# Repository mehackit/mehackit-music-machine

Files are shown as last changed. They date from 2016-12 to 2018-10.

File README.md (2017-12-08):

# Mehackit Music Machine Shield

Music Machine is an Arduino shield that takes in MIDI and controls solenoids and servo motors. You can chain 4 Music Machine Shields and choose the corresponding MIDI notes with a DIP switch. One shield can drive 7 solenoids and 2 servo motors.

See Music Machine Manual for instructions. Currently only in Finnish.

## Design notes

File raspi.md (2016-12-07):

# Raspberry Pi

## Connecting with SSH via ethernet on OSX

- IP = 	192.168.2.2

- Install XQuartz

- Check internet preferences

- Plug the ethernet cable, plug power to the Raspberry Pi

- Terminal: ```ssh -X pi@192.168.2.2```

- Password: raspi

- Copy local pd-path to raspi:

  - Open a new terminal tab on your own computer and locate the file you want to send.
  - ```scp patch.pd pi@192.168.2.2:/some/remote/directory/ ```

- Open the patch on raspi:

  - ```pd-extended patch.pd```

- Open the patch on startup:

  - open .bashrc: ```nano ~/.bashrc```
  - add: ```pd-extended -nogui /path/to/patch.pd```

- Reboot: ```sudo reboot```

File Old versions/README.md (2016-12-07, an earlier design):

# Mehackit Music Machine

## V1

https://vimeo.com/158470330

The first incarnation of the Mehackit music machine was at the Espoo Museum of Modern Art during the Mehackit Art Hack event. 

There's a Pure Data sequencer running on the Raspberry Pi, that sends serial messages to the chan of Arduinos. Each arduino checks if the message belongs to them and either triggers a corresponding solenoid/motor or passes the message forward.

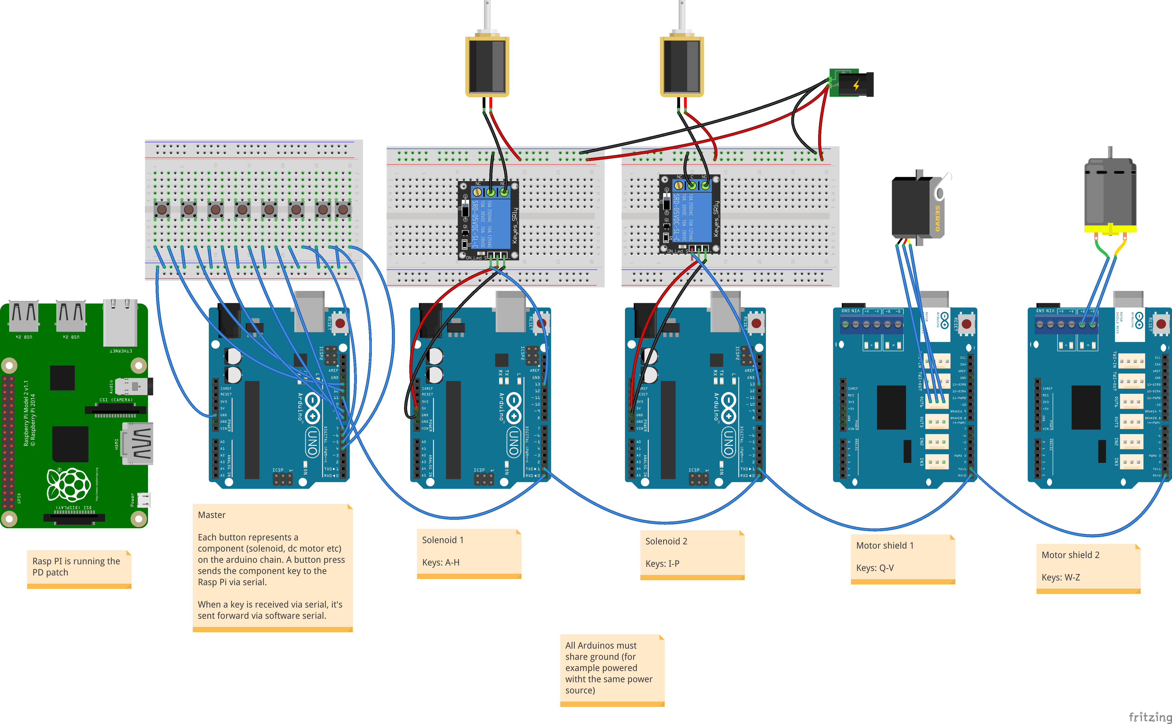
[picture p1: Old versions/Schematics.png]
layout


 The controller looked like this:

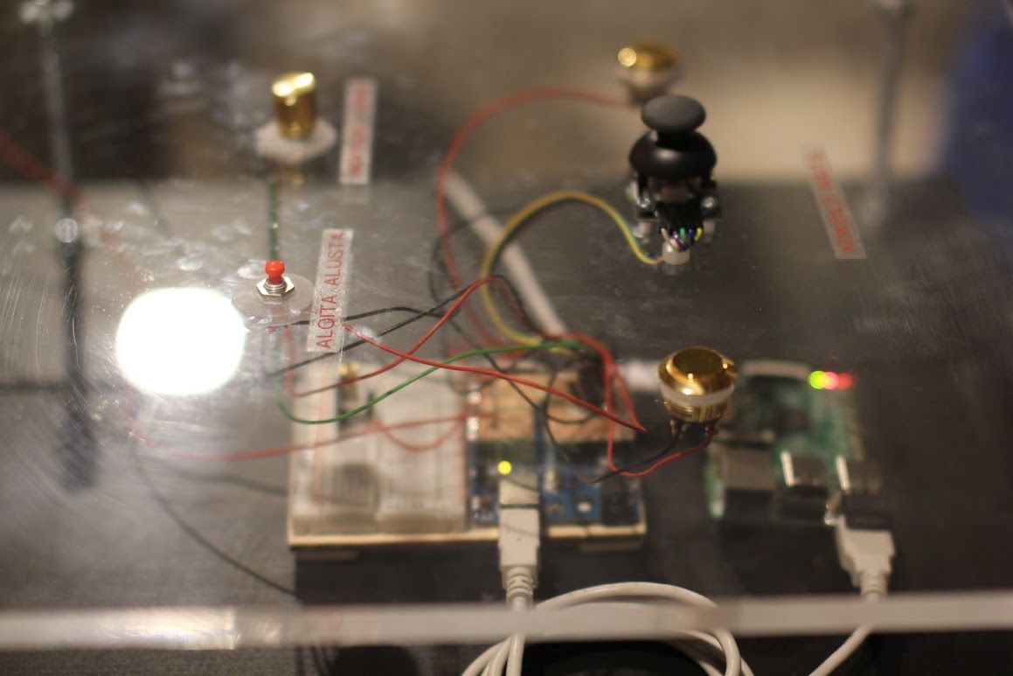
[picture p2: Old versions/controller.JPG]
controller
 

This is the finished installation:

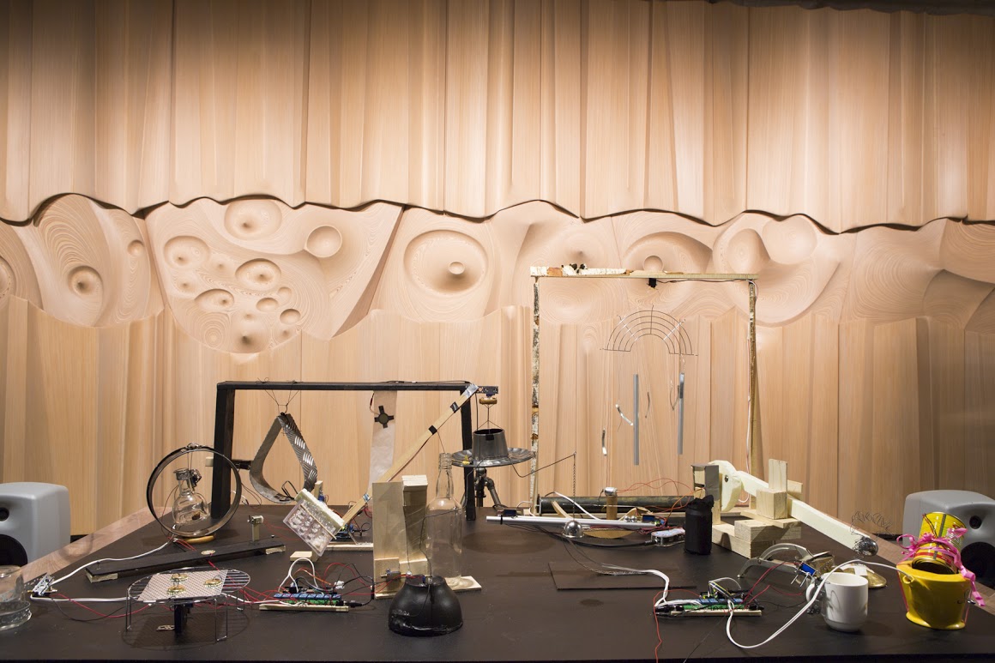
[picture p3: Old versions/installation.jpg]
installation


## V2

New version of the music machine, now with more buttons!

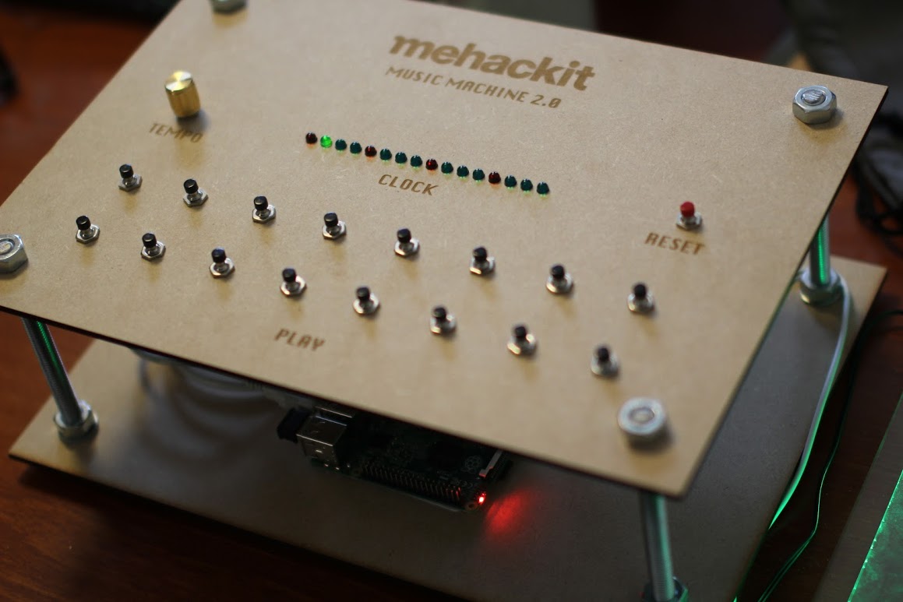
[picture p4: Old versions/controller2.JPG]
controller2


## V3

New version of the music machine, now with less buttons! 

https://vimeo.com/194648696

This version has four knobs that each control a pair of solenoids. The knobs choose from 10 different predefined patterns. The patterns mimic house-like kick, snare, hi-hat and percussion patterns.

## music_machine_v3

The inspiration came from a Max for Live device called Instant Haus by Alexkid. The aim for the controller is to make the installation sound good immediately when a user twists the knobs but still offer enough control to express themselves and play the installation.

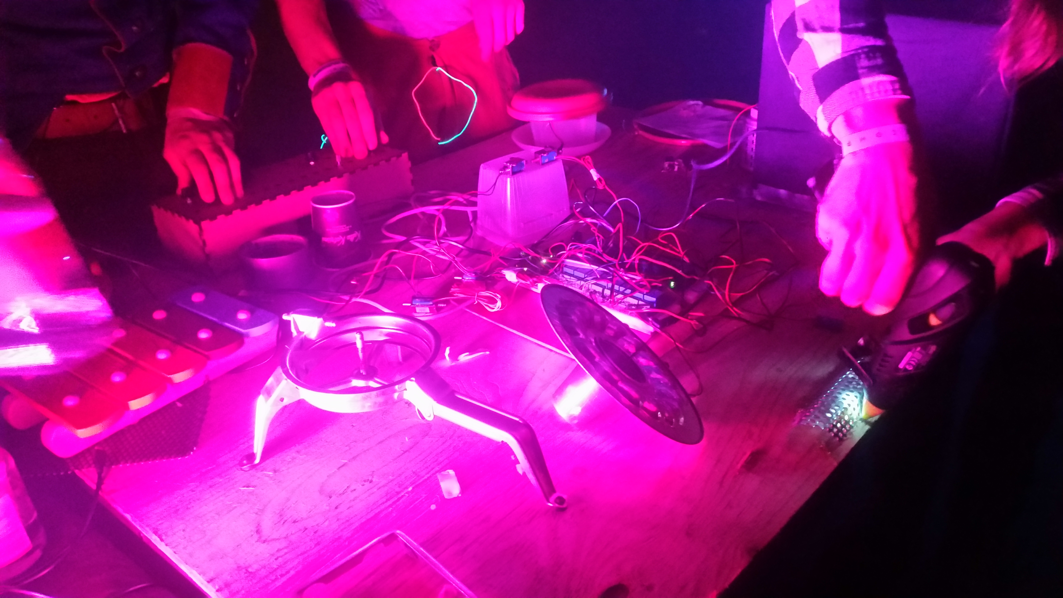
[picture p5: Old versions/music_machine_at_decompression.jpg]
music_machine_at_decompression


This version uses Teensy 3.0 to read the knobs. The Teensy is set up as an USB-MIDI device so it communicates with the Pure Data patch running on Raspberry Pi via MIDI. The Pd-patch then sends the 'notes' to the Arduino as chars via serial.

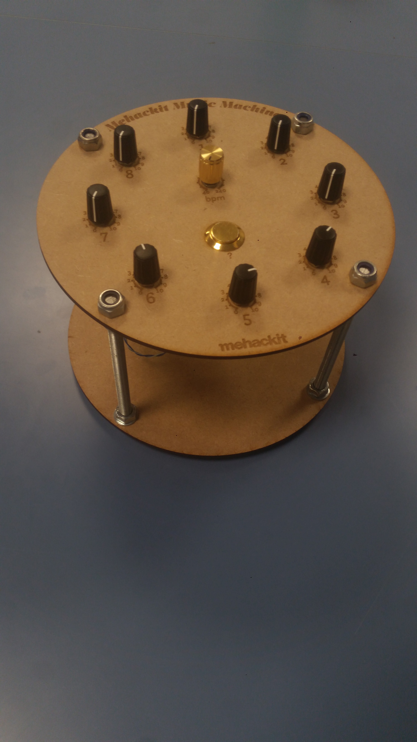
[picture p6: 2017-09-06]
controller4.jpg

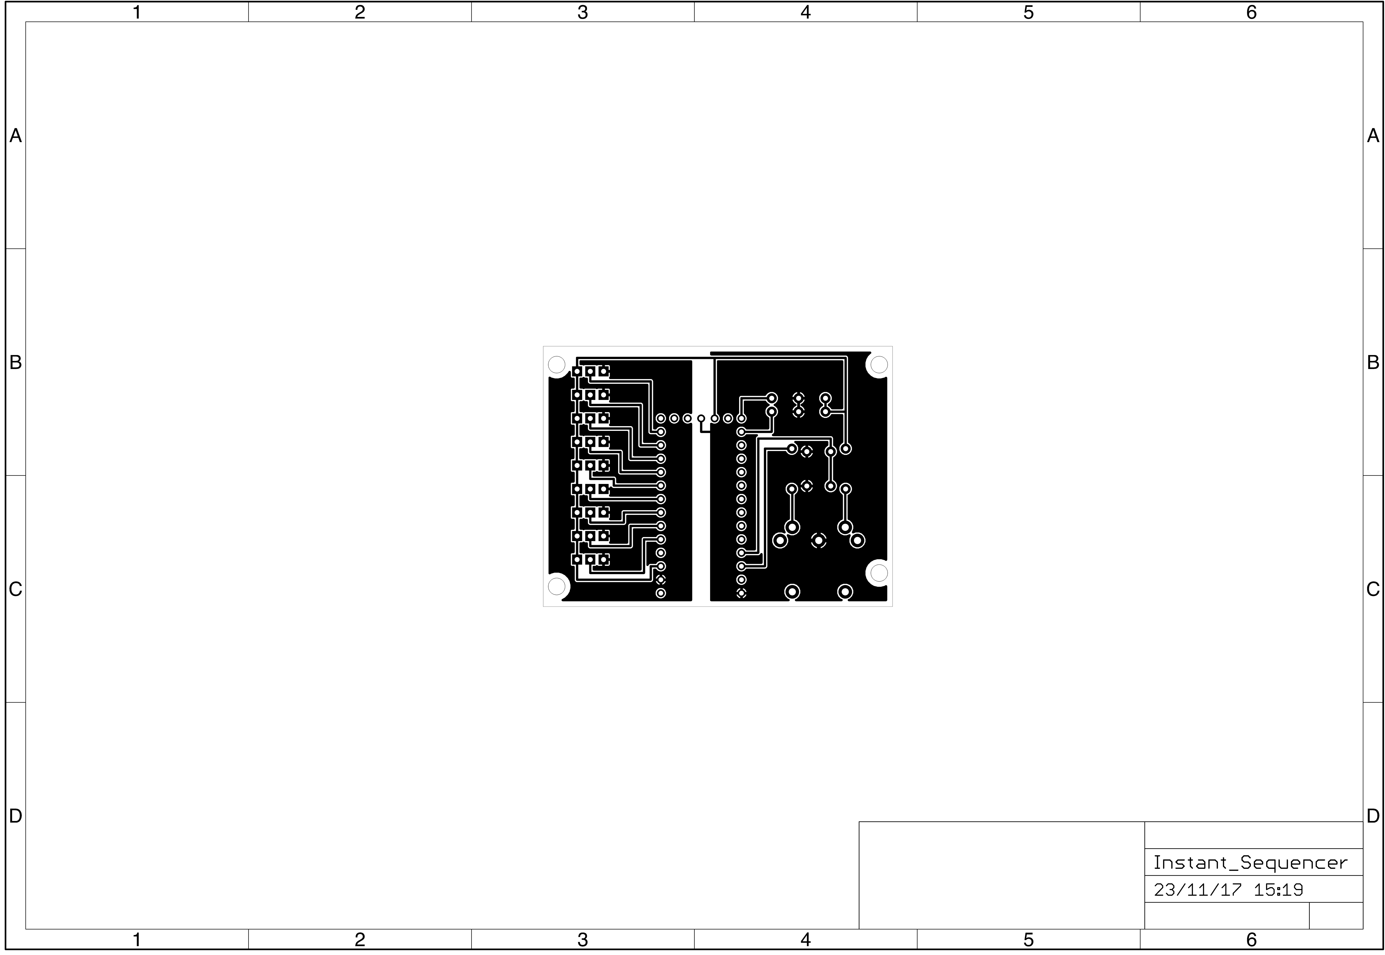
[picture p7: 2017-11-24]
PCB Files/Sequencer PCB.png

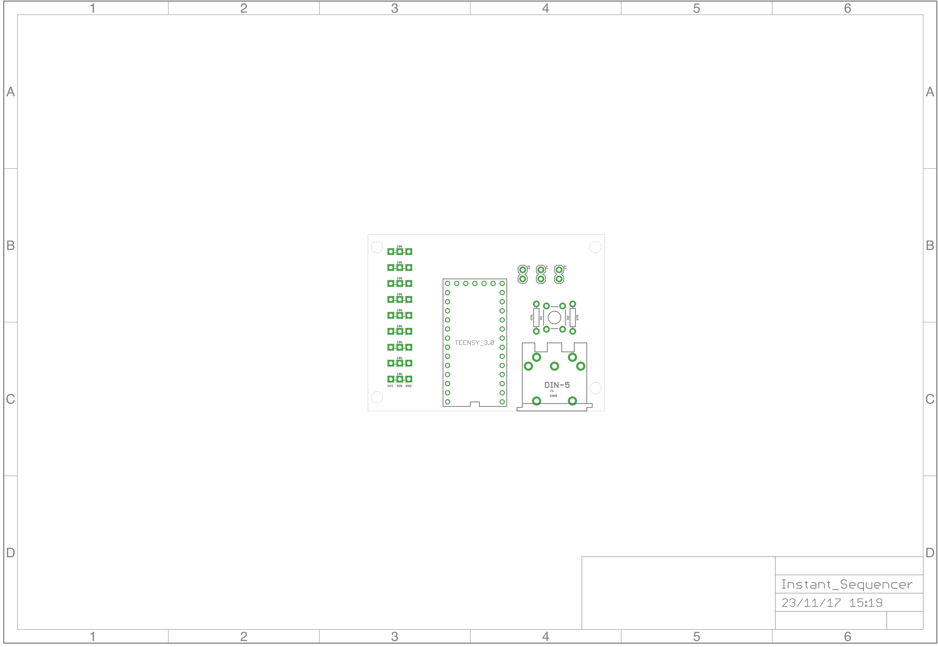
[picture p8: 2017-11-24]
PCB Files/Sequencer PCB placement.png

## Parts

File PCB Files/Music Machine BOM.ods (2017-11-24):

Qty | Package size | Value | TME.EU LINK | Name
1 | 2 | 2 Poles | https://www.tme.eu/en/details/ds-02/dip-switches/ninigi/ | 2 DIP SWITCH
2 | 50 | 10uF | https://www.tme.eu/en/details/ce-1_50sp/85c-tht-electrolytic-capacitors/sr-passives/ | CAP
1 | 1 | ULN2003AN | https://www.tme.eu/en/details/uln2003an/drivers-integrated-circuits/texas-instruments/ | DARLINGTON ARRAY
2 | 1 | MIDI IN, MIDI THROUGH | https://www.tme.eu/en/details/mab5shsw/din-connectors/hirschmann/931744500-mab-5-sh-sw/ | DIN MIDI
1 | 20 | 1N914 | https://www.tme.eu/en/details/1n914tr/tht-universal-diodes/on-semiconductor-fairchild/ | DIODE
7 | 10 | 1N4001 | https://www.tme.eu/en/details/1n4001-dio/tht-universal-diodes/diotec-semiconductor/1n4001/ | DIODE
1 | 10 | DIP16 SOCKET | https://www.tme.eu/en/details/icvt-16p/standard-dip-sockets/connfly/ds1009-16at1nx/ | DIP SOCKET
2 | 5 | RED | https://www.tme.eu/en/details/osnr3134a/tht-leds-3mm/optosupply/ | LED
1 | 10 | SPST | https://www.tme.eu/en/details/tact-64n-f/microswitches-tact/ninigi/ | Momentary Switch
7 | 1 | CL1382B | https://www.tme.eu/en/details/cl1382/jack-connectors/cliff/s6bb-cl1382/ | MONO JACK
1 | 1 | 6N138 | https://www.tme.eu/en/details/6n138-l/optocouplers-analog-output/liteon/6n138/ | OPTOCOUPLER
5 | 10 | 1X10 | https://www.tme.eu/en/details/zl201-10g/pin-headers/connfly/ds1021-1_10sf11/ | Pin Header
2 | 1 | DC 5,5/2,5 | https://www.tme.eu/en/details/pj-102bh/dc-power-connectors/ | POWER JACK
1 | 5 | DC 5,5/2,5 | https://www.tme.eu/en/details/pc-004/dc-power-connectors/ | POWER PLUG
1 | 1 | 12V 1A DC 5,5/2,5 | https://www.tme.eu/en/details/zsi-50030/wall-mounted-power-supplies/qoltec/50030/ | Power supply
1 | 100 | 10k | https://www.tme.eu/en/details/m0.4w-10k/04w-metal-film-tht-resistors/royal-ohm/mff04ff1002a5/ | Resistor
5 | 100 | 220R | https://www.tme.eu/en/details/m0.4w-220r/04w-metal-film-tht-resistors/royal-ohm/mff04ff2200a5/ | RESISTOR
1 | 100 | 470R | https://www.tme.eu/en/details/m0.4w-470r/04w-metal-film-tht-resistors/royal-ohm/mff04ff4700a50/ | RESISTOR
7 | 1 | 12V 0.4A Push/Pull Solenoid |  | Solenoid
1 | 2 | LM7805 | https://www.tme.eu/en/details/lm7805act/unregulated-voltage-regulators/on-semiconductor-fairchild/ | VOLTAGE REGULATOR
7 | 2 | MONO PLUG | https://www.tme.eu/en/details/jc-139/jack-connectors/ | MONO PLUG

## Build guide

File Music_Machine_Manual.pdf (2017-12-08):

# MUSIC MACHINE MANUAL

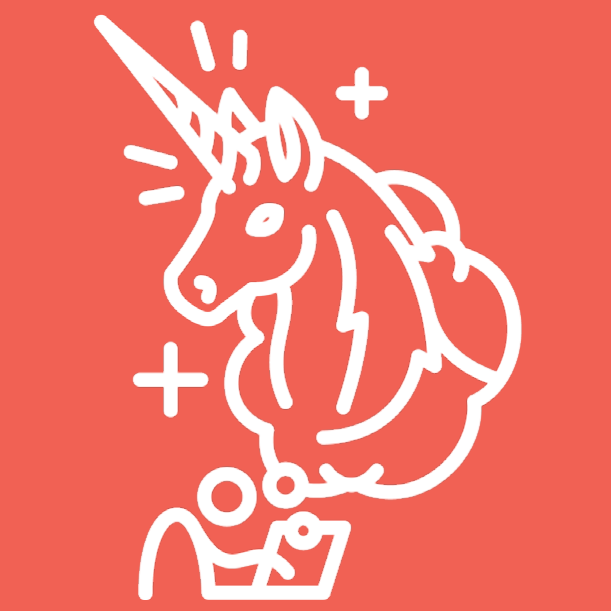
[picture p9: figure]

# MUSIC MACHINE

Music Machine on työkalu ääniveistosten luomiseen. Se kannustaa tutkimaan arkipäiväisten esineiden ja objektien äänimaailmaa muuttaen tavanomaiset asiat perkussiivisiksi soittimiksi.

Music Machine Shield toimii yhdessä Arduino Uno yhteensopivan mikrokontrollerin (esimerkiksi Mehackit Maker Board) kanssa ja vastaanottaa MIDI-viestejä esimerkiksi tietokoneelta tai MIDI-koskettimista.

Tämä opas esittelee Music Machine työpajarungon, käyttöohjeet sekä rakennusohjeet. Uusimmat päivitykset löytyvät Music Machinen github-sivuilta, osoitteesta github.com/mehackit/mehackit-music-machine. (https://github.com/mehackit/mehackit-music-machine/)

# Sisällysluettelo

Työpajan kulku | 1
Käyttöohjeet | 3
Rakennusohjeet | 5
Esimerkkiasennus | 7

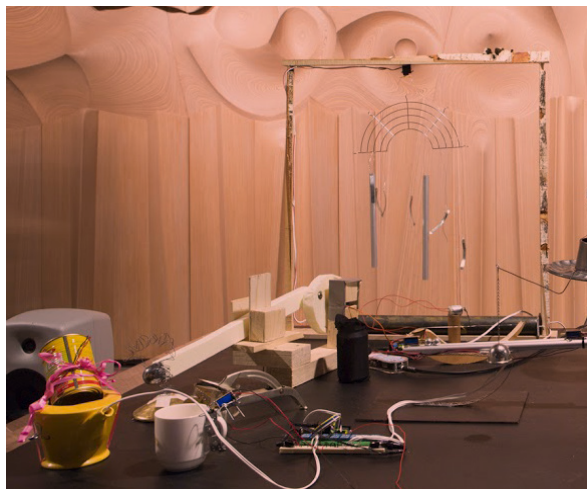
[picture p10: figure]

# Tarvikkeet

Määrä | Nimi
1 | Music Machine Shield PCB
1 | 10kΩ vastus (https://www.tme.eu/en/details/m0.4w-10k/04w-metal-film-tht-resistors/royal-ohm/mff04ff1002a5/)
5 | 330Ω vastus (https://www.tme.eu/en/details/m0.4w-220r/04w-metal-film-tht-resistors/royal-ohm/mff04ff2200a5/)
1 | 470Ω vastus (https://www.tme.eu/en/details/m0.4w-470r/04w-metal-film-tht-resistors/royal-ohm/mff04ff4700a50/)
2 | 10uF kondensaattori (https://www.tme.eu/en/details/ce-1_50sp/85c-tht-electrolytic-capacitors/sr-passives/)
1 | 1N914 vdiodi (https://www.tme.eu/en/details/1n914tr/tht-universal-diodes/on-semiconductor-fairchild/)
7 | 1N4001 diodi (https://www.tme.eu/en/details/1n4001-dio/tht-universal-diodes/diotec-semiconductor/1n4001/)
1 | LM7805 regulaattori (https://www.tme.eu/en/details/lm7805act/unregulated-voltage-regulators/on-semiconductor-fairchild/)
1 | 2 DIP-kytkin (https://www.tme.eu/en/details/ds-02/dip-switches/ninigi/)
1 | ULN2003AN darlington array IC (https://www.tme.eu/en/details/uln2003an/drivers-integrated-circuits/texas-instruments/)
1 | DIP16 kanta (https://www.tme.eu/en/details/icvt-16p/standard-dip-sockets/connfly/ds1009-16at1nx/)
2 | DIN-midi -liitin (https://www.tme.eu/en/details/mab5shsw/din-connectors/hirschmann/931744500-mab-5-sh-sw/)
2 | 3mm LED (https://www.tme.eu/en/details/osnr3134a/tht-leds-3mm/optosupply/)
1 | SPST painonappi (https://www.tme.eu/en/details/tact-64n-f/microswitches-tact/ninigi/)
1 | 6N138 optocoupler IC (https://www.tme.eu/en/details/6n138-l/optocouplers-analog-output/liteon/6n138/)
5 | 1x10 piikkirima (https://www.tme.eu/en/details/zl201-10g/pin-headers/connfly/ds1021-1_10sf11/)
2 | DC 5,5/2,5 -liitin (https://www.tme.eu/en/details/pj-102bh/dc-power-connectors/)
7 | 3,5mm mono-liitin (https://www.tme.eu/en/details/cl1382/jack-connectors/cliff/s6bb-cl1382/)
7 | 3,5mm mono-plugi (https://www.tme.eu/en/details/jc-139/jack-connectors/)
Muu
1 | Arduino Uno / Maker Board
1 | 12V 1A DC 5,5/2,5 Virtalähde (https://www.tme.eu/en/details/zsi-50030/wall-mounted-power-supplies/qoltec/50030/)
7 | 12V olenoidi
1 | MIDI-soitin DIN lähdöllä. (Esim Mu-sic Machine Sequencer)
1 | DIN-midi kaapeli
| Astioita,romua ym. soittimiksi

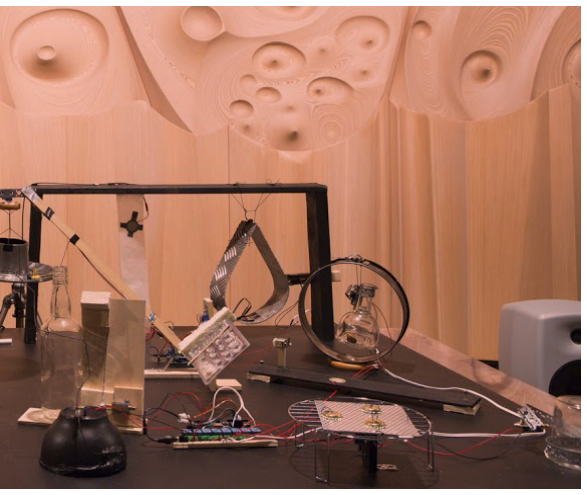
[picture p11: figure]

Työpajan tavoitteena on tutustua ääneen ilmiönä, herkistyä ympäröivien äänien kuuntelemiselle ja analysoinnille sekä toteuttaa kokeellinen ääniveistos kierrätysmateriaalein.

Teemaa voi jatkaa tutustumalla taiteilijoihin, kuten Jean Tinguely, Thessia Machado, Peter Vogel ja Alexander Calder, sekä tutustumalla tarkemmin Arduino-ympäristöön osoitteessa learn.mehackit.org

Aloitus (5min)
Toivota osallistujat tervetulleeksi ja esittäydy. Kerro työpajan sisällöstä ja näytä esimerkkinä yksi solenoidilla tehty soitin. Kysy osallistujien musiikkiharrastuksista.

Mitä ääni on (10min)
Pyydä osallistujia määrittelemään ääni. Ääni syntyy, kun jokin pinta värähtelee ja välittäjäaine (esimerkiksi ilma) välittää värähtelyn kuulijan korvaan. Työpajassa ääni syntyy, kun moottori kopauttaa esinettä, ja esine värähtelee.

Miten ääntä voi kuvailla? Työpajajassa ääntä kuvaillaan kolmella ominaisuudella: äänenkorkeus, voimakkuus sekä sävy. Tee seuraavaksi kaksi kuunteluharjoitusta, jotka puretaan kuvailemmalla kuultuja ääniä edellä mainituilla ominaisuuksilla.

Kuunteluharjoitus 1: Jokainen sulkee silmänsä ja kuuntelee ympäröiviä ääniä 60 sekunnin ajan. Kysy harjoituksen jälkeen, mitä ääniä osallistujat kuulivat.

Kuunteluharjoitus 2: Jokainen sulkee silmänsä ja kuuntelee ympäröiviä ääniä 60 sekunnin ajan sekä tuottaa yhden äänen harjoituksen aikana.

Soittimen rakennus (20min)
Tehtänä on tutkia ympäristöstä löytyvien esineiden akustisia ominaisuuksia ja rakentaa esineestä soitin moottorin avulla. Kannusta osallistujia pohtimaan äänen ominaisuuksia. Esimerkiksi bassorumpu on matala, kovaääninen ja kumiseva. Bassorumpua muistuttavan äänen

# TYÖPAJAN KULKU

luomiseksi pitäisi siis käyttää kookasta ja matalaäänistä esinettä.

Näytä esimerkkinä, miten moottorin voi kiinnittää esineesen. Jaa osallistujat pareihin ja anna jokaiselle parille yksi moottori. Kun sopiva esine löytyy, pari voi viimeistellä ja koristella soittimensa. Osoita pöytä, johon valmiit soittimet tuodaan ja johon installaatio rakentuu. Auta valmiita pareja kiinnittämään soittimen moottorin johdot Music Machineen.

Loppukonsertti (15min)
Kerää osallistujat yhteen, kun soittimet ovat valmiina. Pyydä vapaaehtoinen, joka pääsee esittämään ensi-esityksen. Esityksen jälkeen kuunnellaan vielä jokainen soitin erikseen ja tekijät pääsevät kertomaan luomuksestaan.

Esittelyjen jälkeen jokainen pääsee vuorollaan kokeilemaan laitteen käyttöä.

Lopetus (5min)
Siivoa lopuksi yhdessä osallistujien kanssa pahimmat sotkut. Kiitä työpajasta ja kannusta kuuntelemaan ympäristön ääniä esimerkiksi rullaportaissa, luonnossa, julkisissa liikennevälineissä jne.

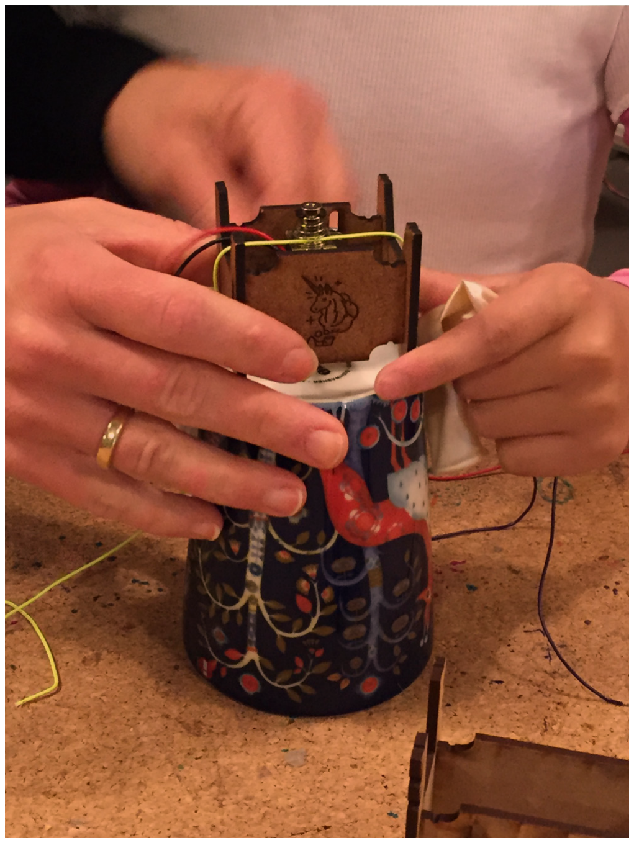
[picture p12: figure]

Lataa Arduino IDE osoitteesta arduino.cc. (https://www.arduino.cc/en/Main/Software) Lataa tiedost 'Music_Machine_Controller. ino' onoitteesta github.com/mehackit/mehackit-music-machine. (https://github.com/mehackit/mehackit-music-machine/) Kytke Arduino-yhteensopiva mikrokontrolleri tietokoneesen USB-johdolla, avaa edellä mainittu tiedosto Arduino IDE:llä ja lataa ohjelma mikrokontrollerille.

Paina Music Machine Shield varovasti mikrokontrollerin päälle. Valitse dip-kytkimellä kuunneltavien nuottien alue ja kytke MIDI-piuha MIDI-lähteeseen, kuten sekvensseriin, koskettimiin tai tietokoneeseen. Dip-kytkimen käyttö selitetään tarkemmin sivun lopussa.

Kytke solenoidit 3,5mm liittimillä s-kirjaimella merkittyihin lähtöihin ja servo-moottorit piikkirimaliittimiin. Varmista, että servo-moottorin liitännät menevät oikein.

Liitä lopuksi virtalähde Music Machine Shieldiin.

Nuottialueen valitseminen

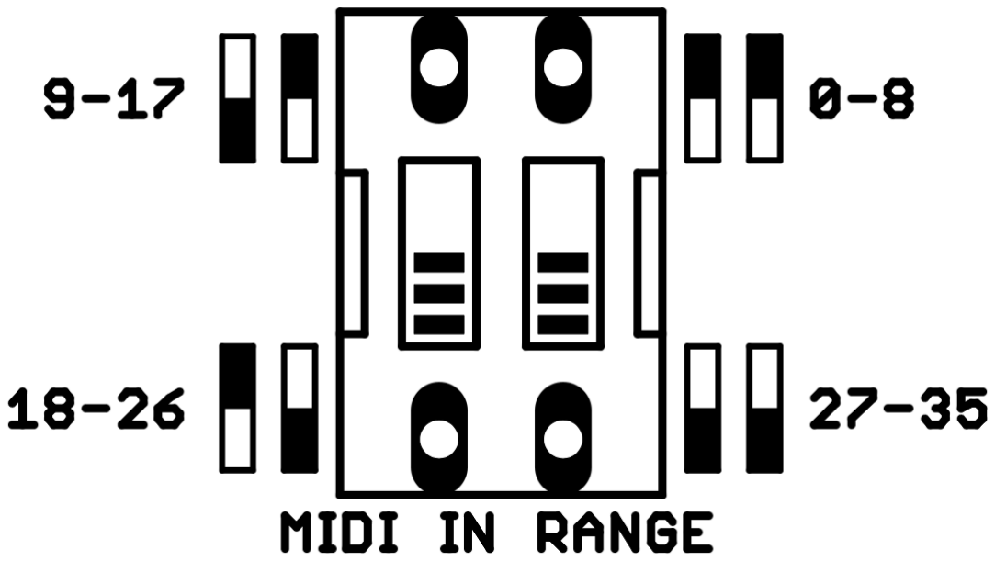
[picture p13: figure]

Nuottialue valitaan asettamalla dip-kytkin yhteen neljästä mahdollisesta asennosta. Molempien liukujen ollessa ylhäällä, MIDI-nuotit 0-8 laukaisevat solenoidin tai moottorin. Asentoa vastaavat nuottialueet on merkattu kytkimen viereen. Mikrokontrolleri pitää käynnistää uudestaan kytkimen asennon muuttamisen jälkeen.

Halutessasi voit ketjuttaa usean soittimen MIDI-trough liitännän avulla ja asettaa soittimet kuuntelemaan eri nuottialueita.

# KÄYTTÖ-OHJEET

# MIDI-sekvensseri

Voit käyttää Music Machinen kanssa mitä tahansa MIDI-laitetta, jossa on lähtö DIN-kaapelille:

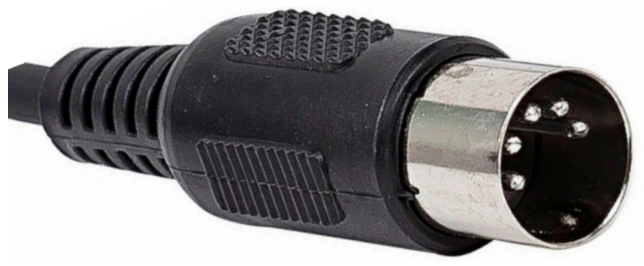
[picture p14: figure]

Useissa koskettimissa voi olla DIN-lähtö. Tietokoneesen voi liittää ulkoisen äänikortin tai MIDI-liitännän, jonka avulla eri musiikkiohjelmistoista voi lähettää MIDI-nuotteja.

Edellä mainitusta github-osoitteesta (https://github.com/mehackit/mehackit-music-machine/) löytyy lisäksi varta vasten Music Machinelle tehty MIDI-sekvensseri:

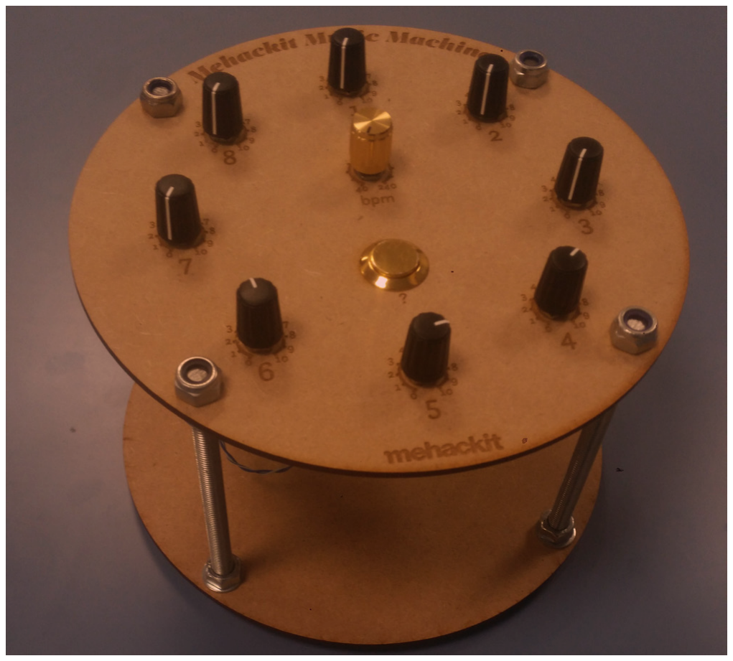
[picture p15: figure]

Jokaisella ympyrän kehällä olevalla nuppilla voidaan valita yksi kymmenesta annalta määritellystä rytmistä. Nuppi 0 lähettää MIDI-nuotteja 0 ja 1, nupi 1 lähettää nuotteja 2 ja 3, nuppi 2 nuotteja 4 ja 5 ja niin edelleen.

Keskimmäisellä nupilla voidaan säätää tempo ja painonappi laukaisee sattumanvaraisen nuotin. Rytmin 'swingiä' voi säätää pitämällä painonappia pohjassa js liikuttaen samalla temponuppia.

# RAKENNUS-OHJEET

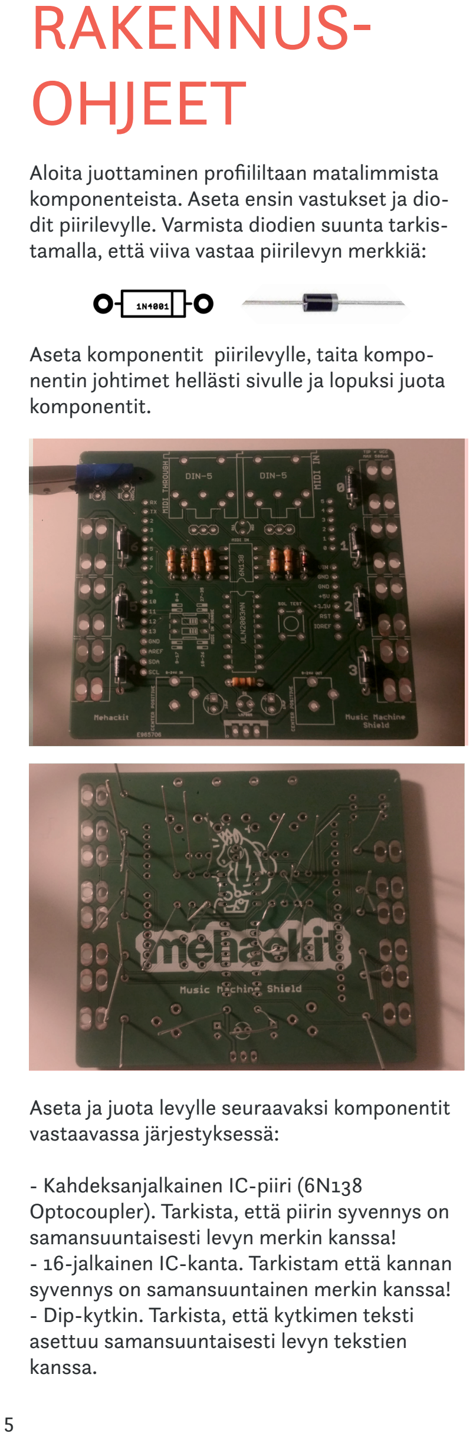
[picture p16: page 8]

Aloita juottaminen profiililtaan matalimmista komponenteista. Aseta ensin vastukset ja diodit piirilevylle. Varmista diodien suunta tarkistamalla, että viiva vastaa piirilevyn merkkiä:

Aseta komponentit piirilevylle, taita komponentin johtimet hellästi sivulle ja lopuksi juota komponentit.

Aseta ja juota levylle seuraavaksi komponentit vastaavassa järjestyksessä:

- Kahdeksanjalkainen IC-piiri (6N138 Optocoupler). Tarkista, että piirin syvennys on samansuuntaisesti levyn merkin kanssa!
- 16-jalkainen IC-kanta. Tarkistam että kannan syvennys on samansuuntainen merkin kanssa!
- Dip-kytkin. Tarkista, että kytkimen teksti asettuu samansuuntaisesti levyn tekstien kanssa.

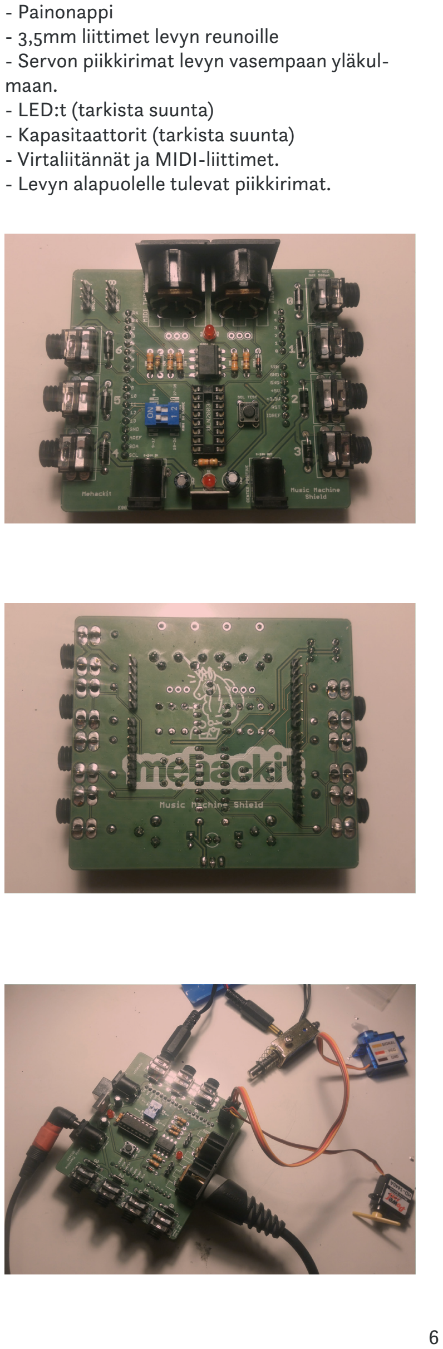
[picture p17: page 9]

- Painonappi
- 3,5mm liittimet levyn reunoille
- Servon piikkirimat levyn vasempaan yläkulmaan.
- LED:t (tarkista suunta)
- Kapasitaattorit (tarkista suunta)
- Virtaliitännät ja MIDI-liittimet.
- Levyn alapuolelle tulevat piikkirimat.

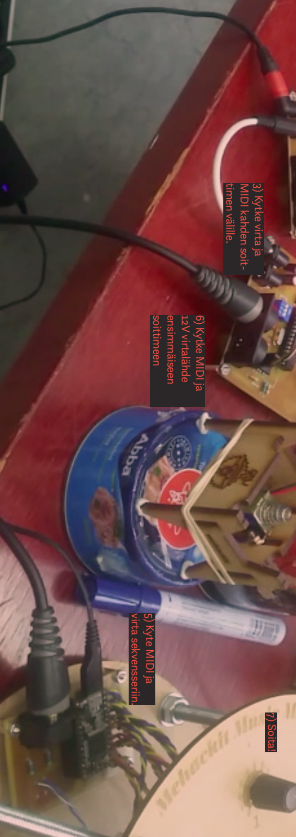
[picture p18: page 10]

MIDI kahden soit

3) Kytke virta ja

timen välille.

virta sekvensseriin.

## 5) Kyte MIDI ja soittimeen

ensimmäiseen

12V virtalähde

6) Kytke MIDI ja
7) Soita!

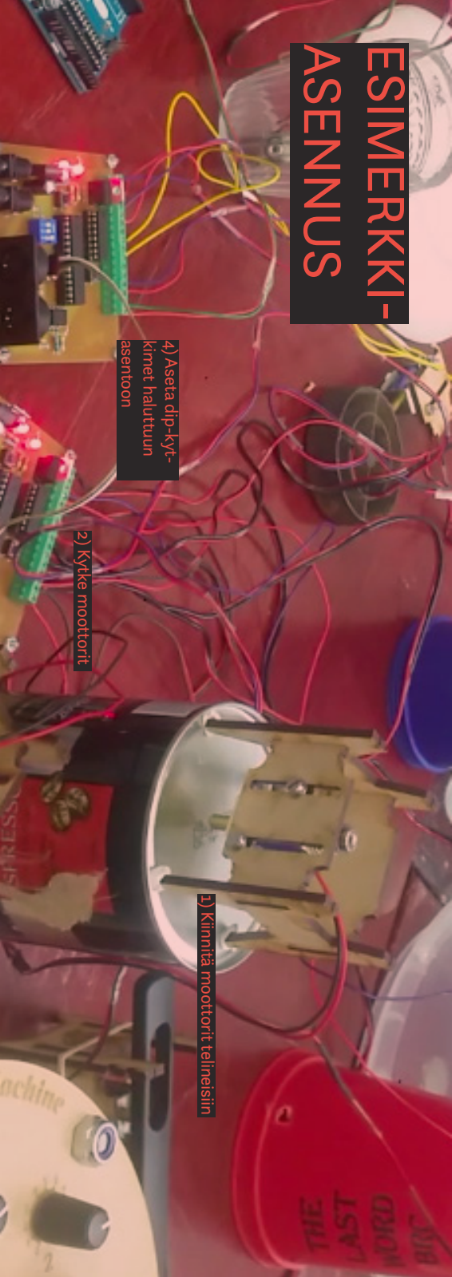
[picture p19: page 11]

# ASENNUS

# ESIMERKKI-

2) Kytke moottorit 1) Kiinnitä moottorit telineisiin 4) Aseta dip-kyt- asentoon kimet haluttuun

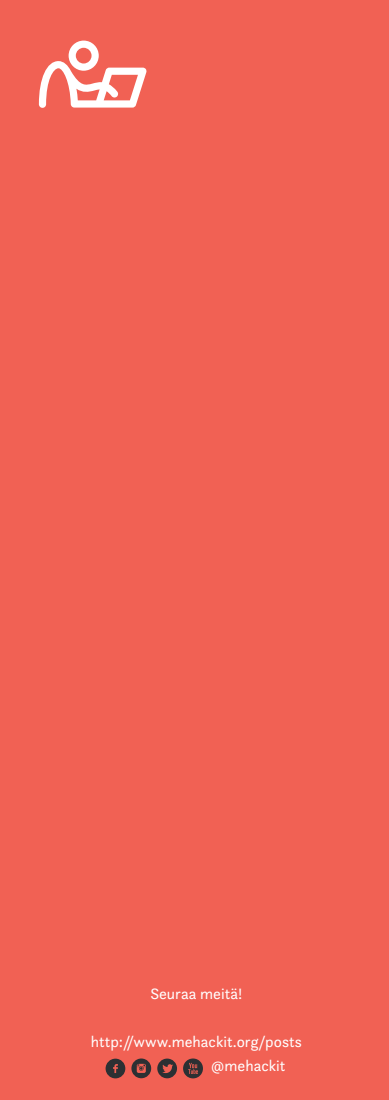
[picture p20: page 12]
Seuraa meitä!; @mehackit

http://www.mehackit.org/posts

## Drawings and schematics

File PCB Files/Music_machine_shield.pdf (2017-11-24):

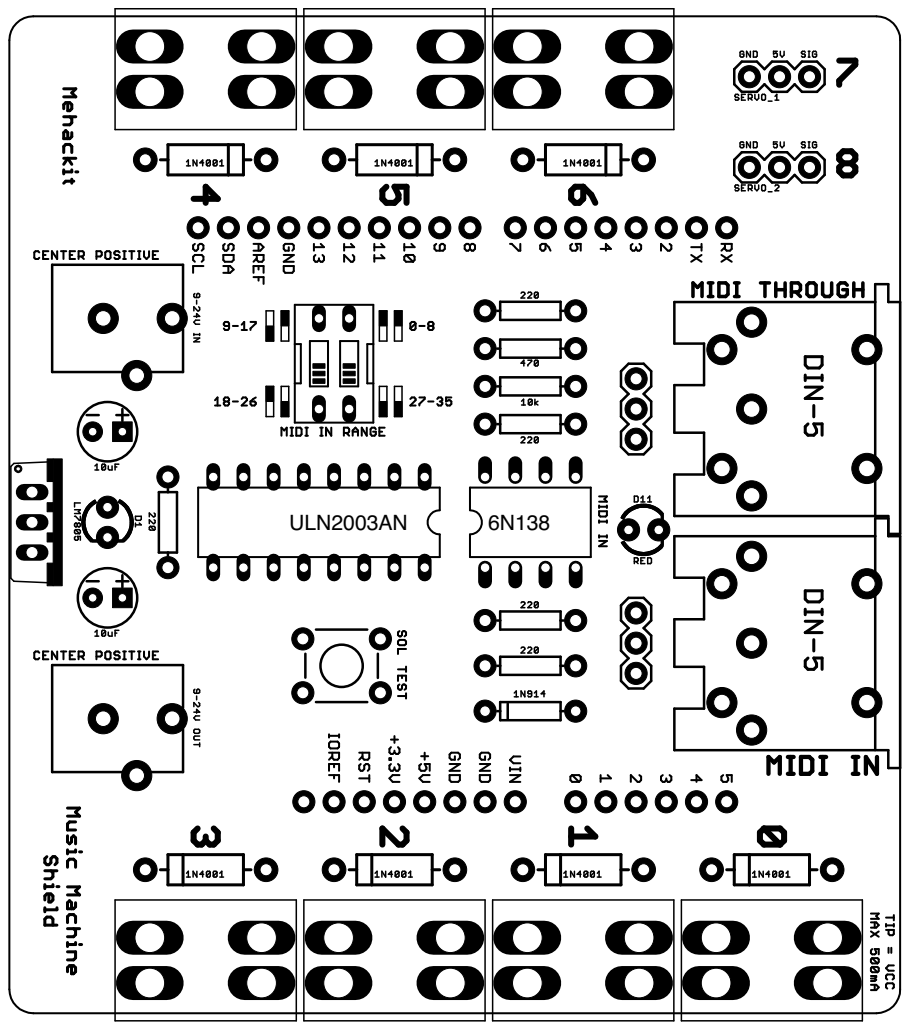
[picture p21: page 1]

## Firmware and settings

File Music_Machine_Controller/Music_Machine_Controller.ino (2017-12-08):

/**
 * Mehackit Music Machine Solenoid Controller
 * 
 * Solenoid controller is a custom ATMEGA board that takes in MIDI
 * and opens VIN current through a corresponding transistor i.e. triggers
 * a salonoid based on the incoming MIDI.
 * 
 * A 3 bit DIP-switch defines the MIDI notes. 0 is notes 0-7, 1 is 8-15 etc.
 * When a MIDI note on is received, a solenoid is triggered for 50ms. All midi
 * is passed to MIDI through.
 * 
 * Otso Sorvettula / Mehackit 2017
 */

#include <MIDI.h>  // Add Midi Library
#include <Servo.h>

#define ledPin 13
#define S1 2
#define S2 3
#define S3 4
#define S4 5
#define S5 6
#define S6 7
#define S7 8
#define ammountOfSolenoids 7
#define ammountOfNotes 9
#define SERVO_1_PIN 9
#define SERVO_2_PIN 10
#define SERVO_1_NOTE 7
#define SERVO_2_NOTE 8

int solenoids[ammountOfSolenoids] = {S1, S2, S3, S4, S5, S6, S7};
int dipPins[2] = {11,12};
int scale = 0;
long notesOff[ammountOfSolenoids];
unsigned long noteLength = 30;
unsigned long now = 0;
boolean servo1AtOrigin = true;
boolean servo2AtOrigin = true;
Servo servo1;
Servo servo2;

//Create an instance of the library with default name, serial port and settings
MIDI_CREATE_DEFAULT_INSTANCE();

void setup() {
  pinMode(S1, OUTPUT);
  pinMode(S2, OUTPUT);
  pinMode(S3, OUTPUT);
  pinMode(S4, OUTPUT);
  pinMode(S5, OUTPUT);
  pinMode(S6, OUTPUT);
  pinMode(S7, OUTPUT);
  pinMode(ledPin, OUTPUT);
  
  for (int i = 0; i < 3; ++i) {
    pinMode(dipPins[i], INPUT_PULLUP);
  }

  for (int i = 0; i < ammountOfSolenoids; i++) {
    notesOff[i] = 0;
  }

  scale = getDipPinsValToInt();

  MIDI.begin(MIDI_CHANNEL_OMNI); //Listen to all MIDI channels
  MIDI.setHandleNoteOn(MyHandleNoteOn);
  MIDI.setHandleNoteOff(MyHandleNoteOff);

  servo1.attach(SERVO_1_PIN);
  servo2.attach(SERVO_2_PIN);
  //servo1.write(0);
  //servo2.write(0);
}

void loop() { // Main loop
  MIDI.read(); // Continuously check if Midi data has been received.
  now = millis();
  for (int i = 0; i < ammountOfSolenoids; i++) {
    if (notesOff[i] < now) {
      digitalWrite(solenoids[i], LOW);
    }
  }
}

int getDipPinsValToInt() {
  byte result = 0;
  for (int i = 0; i < 2; ++i) {
    bool switchOn = digitalRead(dipPins[i]);
    if (switchOn) {
      result = result | (1 << i);
    }
  }
  return (int) result;
}

// MyHandleNoteON is the function that will be called by the Midi Library
// when a MIDI NOTE ON message is received.
// It will be passed bytes for Channel, Pitch, and Velocity
void MyHandleNoteOn(byte channel, byte pitch, byte velocity) {
  digitalWrite(ledPin, HIGH);
  int note = pitch - ammountOfNotes * scale;
  if (note >= 0 && note < ammountOfNotes) {
    if (note < ammountOfSolenoids) {
      digitalWrite(solenoids[note], HIGH);
      notesOff[note] = millis() + noteLength;  
    } else {
      turnServo(note);
    }
  }
}



void turnServo(int note) {
  if (note == SERVO_1_NOTE) {
    if (servo1AtOrigin) {
      servo1.write(150);
    } else {
      servo1.write(30);
    }
    servo1AtOrigin = !servo1AtOrigin;
  } else if (note == SERVO_2_NOTE) {
    if (servo2AtOrigin) {
      servo2.write(150);
    } else {
      servo2.write(30);
    }
    servo2AtOrigin = !servo2AtOrigin;
  }
}

// MyHandleNoteOFF is the function that will be called by the Midi Library
// when a MIDI NOTE OFF message is received.
// * A NOTE ON message with Velocity = 0 will be treated as a NOTE OFF message *
// It will be passed bytes for Channel, Pitch, and Velocity
void MyHandleNoteOff(byte channel, byte pitch, byte velocity) {
  digitalWrite(ledPin, LOW);
}

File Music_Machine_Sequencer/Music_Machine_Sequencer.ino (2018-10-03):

/**
   Mehackit Music Machine Sequencer

   Music Machine Sequencer is a Teensy based sequencer
   with 8 knobs that choose between predefined sequences.



   Otso Sorvettula / Mehackit 2017
*/

#include <AnalogSmooth.h>
#include <MIDI.h>
#include <Bounce.h>
MIDI_CREATE_DEFAULT_INSTANCE();

boolean useFirstNote[8] = {1, 1, 1, 1, 1, 1, 1, 1};

int midiNotes[8][2] = {
  {0, 0},
  {1, 1},
  {2, 2},
  {3, 3},
  {4, 4},
  {5, 5},
  {6, 6},
  {7, 7},
};

// Kick
const bool sequence1[10][16] = {
  {0, 0, 0, 0, 0, 0, 0, 0, 0, 0, 0, 0, 0, 0, 0, 0},
  {1, 0, 0, 0, 0, 0, 0, 0, 1, 0, 0, 0, 0, 0, 0, 0},
  {1, 0, 0, 0, 1, 0, 0, 0, 1, 1, 0, 0, 1, 0, 0, 0},
  {1, 0, 0, 0, 1, 0, 0, 0, 1, 1, 0, 0, 1, 0, 1, 0},
  {1, 0, 0, 0, 1, 0, 0, 0, 1, 0, 0, 0, 1, 0, 0, 1},
  {1, 0, 0, 0, 1, 0, 0, 0, 1, 0, 0, 0, 1, 1, 0, 0},
  {1, 0, 0, 0, 1, 1, 0, 0, 1, 0, 0, 0, 1, 0, 0, 0},
  {1, 0, 0, 0, 1, 1, 0, 0, 1, 0, 0, 0, 1, 0, 1, 0},
  {1, 1, 0, 0, 1, 0, 0, 0, 1, 0, 0, 1, 1, 0, 0, 0},
  {1, 0, 0, 1, 1, 0, 0, 1, 1, 0, 0, 1, 1, 0, 0, 1},
};

// Snare
const bool sequence2[10][16] = {
  {0, 0, 0, 0, 0, 0, 0, 0, 0, 0, 0, 0, 0, 0, 0, 0},
  {0, 0, 0, 0, 1, 0, 0, 0, 0, 0, 0, 0, 1, 0, 0, 0},
  {0, 0, 0, 0, 1, 0, 0, 1, 0, 0, 0, 0, 1, 0, 0, 0},
  {0, 0, 0, 0, 1, 0, 0, 0, 0, 1, 0, 0, 1, 0, 0, 0},
  {0, 0, 0, 0, 1, 0, 0, 0, 0, 0, 0, 0, 1, 1, 0, 0},
  {0, 0, 0, 0, 1, 0, 0, 0, 0, 0, 0, 0, 1, 0, 0, 1},
  {0, 0, 0, 0, 1, 0, 0, 0, 0, 0, 0, 1, 0, 0, 0, 0},
  {0, 0, 0, 0, 1, 0, 0, 0, 0, 0, 0, 1, 1, 0, 0, 0},
  {0, 0, 0, 0, 1, 1, 0, 0, 0, 0, 0, 0, 0, 0, 1, 0},
  {0, 0, 0, 1, 1, 0, 0, 0, 0, 0, 0, 1, 1, 0, 0, 0},
};

// Hihat
const bool sequence3[10][16] = {
  {0, 0, 0, 0, 0, 0, 0, 0, 0, 0, 0, 0, 0, 0, 0, 0},
  {0, 0, 1, 0, 0, 0, 1, 0, 0, 0, 1, 0, 0, 0, 1, 0},
  {0, 0, 1, 1, 0, 0, 1, 1, 0, 0, 1, 1, 0, 0, 1, 1},
  {0, 0, 1, 0, 0, 0, 1, 1, 0, 0, 1, 0, 0, 1, 1, 0},
  {0, 1, 1, 0, 0, 0, 1, 0, 0, 0, 1, 1, 0, 0, 1, 0},
  {0, 0, 1, 0, 0, 1, 0, 1, 0, 0, 1, 0, 0, 0, 1, 0},
  {1, 0, 1, 0, 1, 0, 1, 0, 1, 0, 1, 0, 1, 0, 1, 0},
  {1, 1, 1, 0, 1, 1, 0, 0, 1, 1, 1, 1, 1, 1, 1, 0},
  {1, 1, 0, 1, 1, 1, 0, 1, 1, 1, 0, 1, 1, 1, 0, 1},
  {1, 1, 1, 1, 1, 1, 1, 1, 0, 1, 1, 1, 1, 1, 0, 1},
};

// Perc
const bool sequence4[10][16] = {
  {0, 0, 0, 0, 0, 0, 0, 0, 0, 0, 0, 0, 0, 0, 0, 0},
  {0, 0, 0, 0, 0, 0, 0, 0, 0, 0, 0, 0, 0, 0, 1, 0},
  {0, 0, 0, 0, 0, 0, 0, 0, 0, 0, 0, 0, 0, 1, 0, 1},
  {0, 0, 0, 0, 0, 0, 1, 0, 0, 0, 0, 0, 0, 0, 0, 1},
  {0, 0, 0, 0, 0, 0, 0, 0, 0, 0, 1, 1, 0, 0, 0, 0},
  {0, 0, 0, 0, 0, 1, 0, 0, 0, 0, 0, 1, 0, 0, 0, 0},
  {0, 0, 0, 0, 0, 1, 0, 0, 0, 0, 0, 1, 0, 0, 1, 0},
  {0, 0, 1, 0, 0, 0, 1, 0, 0, 0, 1, 0, 0, 0, 1, 0},
  {0, 0, 1, 0, 0, 0, 1, 0, 0, 0, 1, 0, 0, 0, 1, 1},
  {0, 0, 0, 1, 0, 1, 1, 0, 0, 0, 0, 1, 0, 0, 0, 0},
};


const bool sequence5[10][16] = {
  {0, 0, 0, 0, 0, 0, 0, 0, 0, 0, 0, 0, 0, 0, 0, 0},
  {0, 0, 0, 0, 0, 0, 0, 0, 0, 0, 0, 0, 0, 0, 1, 0},
  {0, 0, 0, 0, 0, 0, 0, 0, 0, 0, 0, 0, 0, 1, 0, 1},
  {0, 0, 0, 0, 0, 1, 0, 0, 0, 0, 0, 0, 0, 0, 0, 1},
  {0, 0, 0, 0, 0, 0, 0, 0, 0, 0, 1, 1, 0, 0, 0, 0},
  {0, 0, 0, 0, 1, 0, 0, 0, 0, 0, 0, 1, 0, 0, 0, 0},
  {0, 0, 0, 0, 1, 0, 0, 0, 0, 0, 0, 1, 0, 0, 1, 0},
  {0, 1, 0, 0, 0, 1, 0, 0, 0, 0, 1, 0, 0, 0, 1, 0},
  {0, 1, 0, 0, 0, 1, 0, 0, 0, 0, 1, 0, 0, 0, 1, 1},
  {0, 0, 1, 0, 1, 1, 0, 0, 0, 0, 0, 1, 0, 0, 0, 0},
};

const bool sequence6[10][16] = {
  {0, 0, 0, 0, 0, 0, 0, 0, 0, 0, 0, 0, 0, 0, 0, 0},
  {1, 0, 0, 0, 0, 0, 0, 0, 1, 0, 0, 0, 0, 0, 0, 0},
  {1, 0, 0, 0, 1, 0, 0, 0, 1, 1, 0, 0, 1, 0, 0, 0},
  {1, 0, 0, 0, 1, 0, 0, 0, 1, 1, 0, 0, 1, 0, 1, 0},
  {1, 0, 0, 0, 1, 0, 0, 0, 1, 0, 0, 0, 1, 0, 0, 1},
  {1, 0, 0, 0, 1, 0, 0, 0, 1, 0, 0, 0, 1, 1, 0, 0},
  {1, 0, 0, 0, 1, 1, 0, 0, 1, 0, 0, 0, 1, 0, 0, 0},
  {1, 0, 0, 0, 1, 1, 0, 0, 1, 0, 0, 0, 1, 0, 1, 0},
  {1, 1, 0, 0, 1, 0, 0, 0, 1, 0, 0, 1, 1, 0, 0, 0},
  {1, 0, 0, 1, 1, 0, 0, 1, 1, 0, 0, 1, 1, 0, 0, 1},
};
const bool sequence7[10][16] = {
  {0, 0, 0, 0, 0, 0, 0, 0, 0, 0, 0, 0, 0, 0, 0, 0},
  {1, 0, 0, 0, 0, 0, 0, 0, 1, 0, 0, 0, 0, 0, 0, 0},
  {1, 0, 0, 0, 1, 0, 0, 0, 1, 1, 0, 0, 1, 0, 0, 0},
  {1, 0, 0, 0, 1, 0, 0, 0, 1, 1, 0, 0, 1, 0, 1, 0},
  {1, 0, 0, 0, 1, 0, 0, 0, 1, 0, 0, 0, 1, 0, 0, 1},
  {1, 0, 0, 0, 1, 0, 0, 0, 1, 0, 0, 0, 1, 1, 0, 0},
  {1, 0, 0, 0, 1, 1, 0, 0, 1, 0, 0, 0, 1, 0, 0, 0},
  {1, 0, 0, 0, 1, 1, 0, 0, 1, 0, 0, 0, 1, 0, 1, 0},
  {1, 1, 0, 0, 1, 0, 0, 0, 1, 0, 0, 1, 1, 0, 0, 0},
  {1, 0, 0, 1, 1, 0, 0, 1, 1, 0, 0, 1, 1, 0, 0, 1},
};
const bool sequence8[10][16] = {
  {0, 0, 0, 0, 0, 0, 0, 0, 0, 0, 0, 0, 0, 0, 0, 0},
  {1, 0, 0, 0, 0, 0, 0, 0, 1, 0, 0, 0, 0, 0, 0, 0},
  {1, 0, 0, 0, 1, 0, 0, 0, 1, 1, 0, 0, 1, 0, 0, 0},
  {1, 0, 0, 0, 1, 0, 0, 0, 1, 1, 0, 0, 1, 0, 1, 0},
  {1, 0, 0, 0, 1, 0, 0, 0, 1, 0, 0, 0, 1, 0, 0, 1},
  {1, 0, 0, 0, 1, 0, 0, 0, 1, 0, 0, 0, 1, 1, 0, 0},
  {1, 0, 0, 0, 1, 1, 0, 0, 1, 0, 0, 0, 1, 0, 0, 0},
  {1, 0, 0, 0, 1, 1, 0, 0, 1, 0, 0, 0, 1, 0, 1, 0},
  {1, 1, 0, 0, 1, 0, 1, 0, 1, 0, 0, 1, 1, 0, 0, 0},
  {1, 0, 0, 1, 1, 0, 0, 1, 1, 0, 0, 1, 1, 0, 0, 1},
};

const int SEQ_LENGTH = 16;
const bool (*sequences[])[16] {
  sequence1,
  sequence2,
  sequence3,
  sequence4,
  sequence5,
  sequence6,
  sequence7,
  sequence8,
  NULL
};

const int tempoPin = A8;
const int pin1 = A0;
const int pin2 = A1;
const int pin3 = A2;
const int pin4 = A3;
const int pin5 = A4;
const int pin6 = A5;
const int pin7 = A6;
const int pin8 = A7;
const int sequencePins[8] = {pin1, pin2, pin3, pin4, pin5, pin6, pin7, pin8};

const int buttonPin = 2;
Bounce pushbutton = Bounce(buttonPin, 10);
byte buttonPressed = true;
float swing = 0; //Swing in percentage
float lastSwing = 0;
float newSwing = 0;

AnalogSmooth asTempo = AnalogSmooth(100);
int tempo = 120;
int newTempo = 120;

long interval;
unsigned long nextPosition = 0;
int position = 0;
int channel = 1;

void setup() {
  Serial.begin(9600);
  MIDI.begin();
  interval = bpmToInterval(tempo);
  pinMode(buttonPin, INPUT_PULLUP);
}
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
